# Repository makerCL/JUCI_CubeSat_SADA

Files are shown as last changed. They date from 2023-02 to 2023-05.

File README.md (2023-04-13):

## CubeSat Solar Array Drive - Cal Poly Senior Project

This repository presents the development and proposed design of a deployable Solar Array Drive Assembly that could be flown on space-bound CubeSat missions. Our project addresses the need for reliable sources of power in spacecraft and other missions beyond the Earth's atmosphere. Our goal is to create a two degree of freedom SADA, including the passive retainment, deployment, and axial rotation of a solar array to track the sun during the CubeSat’s orbit. It will have the ability to be easily adapted and integrated into other CubeSat builds but does not include other subsystems necessary for full satellite. The scope includes three main areas: the design and manufacture of a 90-degree locking hinge that allows multiple solar arrays to deploy from the stored launch state, the controlled axial rotation of the deployed panels, and the electronics necessary to manage these features with the potential for sun tracking algorithms. 

Subsystem Managers:
- Miles - Electronics
- Gavin - Software
- James - Project Management
- Kory  - Mechanical
- Jose  - Mechanical

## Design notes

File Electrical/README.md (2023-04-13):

This file details the electrical subsystems
Author: Miles Alderman

##Boards:
- Photodiode Breakout: used for sun sensing with one connected to each solar array
- Pico Shield: Peripherals and connection points that interfaces with a Raspberry Pi Pico

##Accessing the Files
- all project files are in Kicad version 6, which the use will need to use to view them
- Digikey library was imported, available at https://forum.digikey.com/t/importing-the-digi-key-kicad-library-into-kicad-5-0-0/4075
- Custom schematic symbols and footprints are in the "KiCad Libs" folder. These will need to be imported

#SADA Board

##Description
The "SADA BOARD" encompasses all the functionality necessary for the Solar Array Drive Assembly and its components. It would interface with a "Systems Board" through a protocol like I2C or CAN.

##Functionality
- Voltage regulator accepts between 3.7 to 4.2V from an external power supply, which represents a single parallel group of Lithium Ion cells, as would like be present in a CubeSat since about 66% of nano and pico scale satellites implement them.(Bouwmeester and Guo). A battery and battery management system is out of scope for this project.
- Nichrome Wire burner: to burn the fishing line that passively retains the spring-loaded solar arrays, we use Nichrome burn wire. This is necessary since the satellite must be powered off during launch. There are pins used to control the burn signal, one of which is the enable for the PMIC, the other of which controls a Mosfet for connecting power to the Nichrome. In some tests, we found that when the system was powered up from its launch state, if the power supply was turned on with a direct connection to the wire it heated it slower, resulting in less reliable deployment. By having a transistor, we can allow the PMIC to become fully stable, and then open it to heat the wire. This PMIC can then be disable to save power after the wire is burnt. Our tests foudn that about 1.5A was the minimum current to heat the wire enough to cleanly burn the fishing line.
- Attitude Determination Diodes: since in a full CubeSat build there would need to be orientation photodiodes on each corner, the peripherals are provided to do so. This includes a MUX to an ADC channel of the MCU to take this measurement.
    - The photodiodes were connected in reverse bias to the inverting input of an op amp. To take a reading with good resolution, this tiny current must be amplified before reaching an ADC. Transconductance amplifiers are a way to do this, connecting the photodiode to the inverting input of an op-amp, the non-inverting input to ground, and placing a feedback resistor from inverting input to output. A capacitor in parallel with the feedback resistor adds stability by acting as a voltage buffer. Capacitance in the photodiode combined with the feedback resistor naturally create a low pass filter as well. The output voltage of the amplifier can then be connected to an ADC channel of the MCU. The voltage sent to the ADC channel is equal to the photodiode current times the feedback resistor plus the offset voltage at the non-inverting input.
    - It is important to verify the photodiode current is at least an order of magnitude more than the input bias current of the op amp, which roughly doubles with ever 10 deg C increase in temperature.
- Stepper Motor Drivers: Since the stepper motors for axial rotation of the arrays need to be driven from the MCU, a Darlington Transistor array is used to accomplish this. This allows the small current of the MCU GPIO to drive the much higher current needed by a stepper, taken from the 5V supply. Stepper motors are precise, but very power hungry due to _________, so we decided to have MOSFETS that can disconnect from power for when the steppers are not actively changed. This does eliminate some functionality of the steppers, such as fractional stepping, but the resolution of that is far greater than our sensing method's, and thus we couldn't take advantage of it anywyas.
- Breakout board connectors: connectors to the Photodiode Breakout Board are implemented for 2 MUX pins, an ADC channel, power and ground

##Design Considerations 
For full information, please see current design report in the parent folder of the repository. Some key details are listed below
- Were not able to use a "space grade" MCU since they are far too expensive for the price point of this project. We therefore are trying to adapt consumer grade MCUs to fit the needs of this project. This would only protect against total radiation experienced from low energy particles, and not against bit flips. In the systems board, TMR would likely be used. 
- Since this is a prototype and will not be launched into space, we aren't going through the rad hardening. It would be silly to spend extra money for a more specific MCU that wouldn’t work anyways. All the other common MCUs have similar temperature ranges besides the ESP32, although its is still not within range of what we expect a CubeSat to encounter
- Dual Modular Redundancy for these systems?
- In a full system, the battery system would output between about 3.6 - 4.2V if a lithium ion cell chemistry was used. We need to step that down to 3.3V for the RP2040. We chose to use an LDO to power the MCU despite them being less efficient than switching regulators since when the LDOs will use less power when considering the high amount of sleep time of the MCU.
- We decided to use stepper motors despite them being very power hungry. Stepper motors invert  the "locked rotor" issue of dc motors, stepping between locked rotor positions. This means that when the motor is not moving, the coils are still fully energized. This is bad for a CubeSat, where power is extremely scarce. To get around this issue while still utilizing the positional accuracy of stepper motors, we can step the motor and then immediately disconnect the power line so that it stops drawing current. Since the cores of the motor are permenant magnets, the motor remains in the last position even when the motor is off, as long as we do not depend on any partial-stepping functions. 
- USB implemented for the development process, but isn't necessary on a deployed system. It allows the engineer to set it up as a flash device, making it convenient to interface with. The STLINK with SWD and TX/RX pins can be used for all of the functionality in its absence as well. It enables debugging, a serial port, and flashing binary code (such as Micropython) onto the main board.
- The stepper driver boost converters were designed to be able to handle a maximum current of 1A. The stepper motor 28BYJ-48 chosen has a maximum current of approximately 0.28A, so this means that one boost converter could drive 2 motors with a safety factor of 2. This current can easily be increased with minor changes in the supporting circuitry found in the datasheet for the boost converter.
- The darlington transistors were abandoned. They are 45 year old tech, they have pretty substantial current to drive it (power hunger), they have a more substantial voltage drop. Stepper driver chips are much more efficient. 
- Stepper motors were eventually abandoned in favor of a BLDC. https://llis.nasa.gov/lesson/893
- 

SOFTWARE
- NRST Pin exposed to systems board so that software reflash could be triggered externally and passed through I2C instead of SWD. On our board though, we still have teh SWD pins exposed since that is how we will be flashing code. NRST is also helpful as an external reset as it resets the registers and changes the program counter to the reset vector. https://electronics.stackexchange.com/questions/491068/what-is-the-use-of-nrst-pin-in-stm32f401rct6 and p21 of Data sheet

##Citations:
1. J. Bouwmeester, J. Guo, Survey of worldwide pico- and nanosatellite missions, distributions and subsystem technology, Acta Astronautica,
2.  https://www.analog.com/en/technical-articles/optimizing-precision-photodiode-sensor-circuit-design.html

CONCERNS:
- Auxillary photodiode board- if it's just on the panel, it likely will be buffeted with radiation, heat, etc. Need to plan for this

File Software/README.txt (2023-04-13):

The software uses C++ as the compiler. To run code on the Pico, you must first
Download an IDE (I use VS Code) and download a CMake compiler. When writing
software, you first create a main.c file in your working directory, then once
it is written, you have to make a CMakeLists.txt file that includes all the
information CMake needs to compile your code. For reference, look at the 
CMakeLists.txt file in the ADC_Read_script directory. For additional setup, 
refernce this video: https://www.youtube.com/watch?v=B5rQSoOmR5w&ab_channel=Digi-Key
For C++ documentation on the PI, reference the following doxygen pages:
https://raspberrypi.github.io/pico-sdk-doxygen/modules.html

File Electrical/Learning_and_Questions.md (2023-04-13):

## Questions
- separate power supply for ADC?
- is there a difference between power cycling for reset and external reset with NRST pin?
- there seems to be so many different types of resets and conditions... which types matter to us?
- Battery Sag makes Battery input even lower than 3.6V at low SOC?

- Oscillator design
    - Do we need to run this MCU at full speed? (80 MHz)? do we need an external oscillator?
    p11 of oscillator design; Cs is stray capacitance of oscin and oscout pins plus pcb parasitic capacitance

- Double mosfets Too redundant for passive retainment since it only has to work once at the beginning of deployment?
- Clock needs for USB (datasheet p57)
- what would input power be from battery board? Would it be a nominal voltage?
- noise considerations- where are overlapping frequencies? Other design considerations for switching component compatability?
- GIO: which ldo did you use for batt to 3v3 line?

## UPGRADED BOARD
- NRST connected to systems board

## Discussion
- could perhaps use lowpower mode with LSE instead with a lean and mean C code?

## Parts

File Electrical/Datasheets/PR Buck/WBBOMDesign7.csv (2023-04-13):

Part | Manufacturer | Part Number | Quantity | Price ($) | Footprint (mm²) | Description
Rfbb | Vishay-Dale | CRCW0402100KFKED | 1 | 0.01 | 3 | Resistance: 100 kΩ Tolerance: 1.0% Power: 63 mW
Rfbt | Vishay-Dale | CRCW0402232KFKED | 1 | 0.01 | 3 | Resistance: 232 kΩ Tolerance: 1.0% Power: 63 mW
L1 | Vishay-Dale | IHLP1212AEERR22M11 | 1 | 0.63 | 19.32 | L: 220 nH DCR: 11.4 mΩ IDC: 8.5 A
Cin | MuRata | GRM188R60J106ME47D | 2 | 0.03 | 4.68 | Cap: 10 µF Total Derated Cap: 6.6 µF VDC: 6.3 V ESR: 9 mΩ Package: 0603
Cout | MuRata | GRM21BD70J226ME44L | 2 | 0.1 | 6.75 | Cap: 22 µF Total Derated Cap: 38 µF VDC: 6.3 V ESR: 1 mΩ Package: 0805
U1 | Texas Instruments | TPS62867RQYR | 1 | 0.903 | 8.75
Rpgood | Vishay-Dale | CRCW0402100KFKED | 1 | 0.01 | 3 | Resistance: 100 kΩ Tolerance: 1.0% Power: 63 mW

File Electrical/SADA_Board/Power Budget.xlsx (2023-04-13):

Power Budget
Number | Description | Frequency | V_in | Current | Power_total | Efficiency
 | MCU | 8 MHz
 | Passive Retainment Buck | 2.75 MHz
 | Stepper Driver 1 Output
 | Stepper 1 STCK | 1 MHz
 | Stepper Driver 2 Output
 | Stepper 2 STCK | 1 MHz

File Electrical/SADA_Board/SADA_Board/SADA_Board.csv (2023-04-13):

Source: | /Users/milesalderman/Library/CloudStorage/OneDrive-Personal/Documents/Senior Project/JUCI_CubeSat_SADA/Electrical/SADA_Board/SADA_Board/SADA_Board.kicad_sch
Date: | Friday, April 07, 2023 at 02:47:55 PM
Tool: | Eeschema (6.0.11-0)
Generator: | /Applications/KiCad/KiCad.app/Contents/SharedSupport/plugins/bom_csv_grouped_by_value.py
Component Count: | 157
Individual Components:
Item | Qty | Reference(s) | Value | LibPart | Footprint | Datasheet | Category | DK_Datasheet_Link | DK_Detail_Page | Description | Digi-Key_PN | Family | Height | MPN | Manufacturer | Manufacturer_Name | Manufacturer_Part_Number | Mouser Part Number | Mouser Price/Stock | Name | Part | Status
 |  | C1 | 10uF | Device:C | Capacitor_SMD:C_0603_1608Metric | ~ |  |  |  |  |  |  |  | F981A106MMUAJ6
 |  | C2 | 4pF | Device:C | Capacitor_SMD:C_0402_1005Metric | ~ |  |  |  |  |  |  |  | CGA2B2C0G1H060D050BA
 |  | C3 | 100nF | Device:C | Capacitor_SMD:C_0402_1005Metric | ~ |  |  |  |  |  |  |  | GRT155R71C104KE01J
 |  | C4 | 1uF | Device:C | Capacitor_SMD:C_0603_1608Metric | ~ |  |  |  |  |  |  |  | TACL105K016XTA
 |  | C5 | 100nF | Device:C | Capacitor_SMD:C_0402_1005Metric | ~ |  |  |  |  |  |  |  | GRT155R71C104KE01J
 |  | C6 | 100nF | Device:C | Capacitor_SMD:C_0402_1005Metric | ~ |  |  |  |  |  |  |  | GRT155R71C104KE01J
 |  | C7 | 10nF | Device:C | Capacitor_SMD:C_0402_1005Metric | ~ |  |  |  |  |  |  |  | GRT155R71C103KE01J
 |  | C8 | 100nF | Device:C | Capacitor_SMD:C_0402_1005Metric | ~ |  |  |  |  |  |  |  | GRT155R71C104KE01J
 |  | C9 | 4pF | Device:C | Capacitor_SMD:C_0402_1005Metric | ~ |  |  |  |  |  |  |  | CGA2B2C0G1H060D050BA
 |  | C10 | 1nF | Device:C | Resistor_SMD:R_0402_1005Metric | ~ |  |  |  |  |  |  |  | GCM155R71H102KA37J
 |  | C11 | 10nF | Device:C | Capacitor_SMD:C_0402_1005Metric | ~ |  |  |  |  |  |  |  | GRT155R71C103KE01J
 |  | C12 | 10uF | Device:C | Capacitor_SMD:C_0603_1608Metric | ~ |  |  |  |  |  |  |  | GRT188C81A106ME13D
 |  | C13 | 10uF | Device:C | Capacitor_SMD:C_0603_1608Metric | ~ |  |  |  |  |  |  |  | GRT188C81A106ME13D
 |  | C14 | 1.5nF | Device:C | Capacitor_SMD:C_0402_1005Metric | ~ |  |  |  |  |  |  |  | CC0402KRX7R7BB152
 |  | C15 | 10uF | Device:C | Capacitor_SMD:C_0603_1608Metric | ~ |  |  |  |  |  |  |  | GRT188C81A106ME13D
 |  | C16 | 10uF | Device:C | Capacitor_SMD:C_0603_1608Metric | ~ |  |  |  |  |  |  |  | GRT188C81A106ME13D
 |  | C17 | 1uF | Device:C | Capacitor_SMD:C_0603_1608Metric | ~ |  |  |  |  |  |  |  | TACL105K016XTA
 |  | C18 | 1uF | Device:C | Capacitor_SMD:C_0603_1608Metric | ~ |  |  |  |  |  |  |  | TACL105K016XTA
 |  | C19 | 22 uF | Device:C | Capacitor_SMD:C_1210_3225Metric | ~ |  |  |  |  |  |  |  | CGA6P1X7R1C226M250AC |  |  |  |  |  |  | Cout
 |  | C20 | 2.2 uF | Device:C | Resistor_SMD:R_0603_1608Metric | ~ |  |  |  |  |  |  |  | CGA3E1X7S1C225M080AC
 |  | C21 | 22nF | Device:C | Capacitor_SMD:C_0402_1005Metric | ~ |  |  |  |  |  |  |  | AC0402KRX7R7BB223
 |  | C22 | 1nF | Device:C | Resistor_SMD:R_0402_1005Metric | ~ |  |  |  |  |  |  |  | GCM155R71H102KA37J
 |  | C23 | 10nF | Device:C | Resistor_SMD:R_0402_1005Metric | ~ |  |  |  |  |  |  |  | GRT155R71C103KE01J |  |  |  |  |  |  | Cen
 |  | C24 | 22 uF | Device:C | Capacitor_SMD:C_1210_3225Metric | ~ |  |  |  |  |  |  |  | CGA6P1X7R1C226M250AC |  |  |  |  |  |  | Cout
 |  | C25 | 2.2 uF | Device:C | Resistor_SMD:R_0603_1608Metric | ~ |  |  |  |  |  |  |  | CGA3E1X7S1C225M080AC
 |  | C26 | 22nF | Device:C | Capacitor_SMD:C_0402_1005Metric | ~ |  |  |  |  |  |  |  | AC0402KRX7R7BB223
 |  | C27 | 1nF | Device:C | Resistor_SMD:R_0402_1005Metric | ~ |  |  |  |  |  |  |  | GCM155R71H102KA37J
 |  | C28 | 10nF | Device:C | Resistor_SMD:R_0402_1005Metric | ~ |  |  |  |  |  |  |  | GRT155R71C103KE01J |  |  |  |  |  |  | Cen
 |  | C29 | 10uF | Device:C | Capacitor_SMD:C_0603_1608Metric | ~ |  |  |  |  |  |  |  | GRT188C81A106ME13D
 |  | C30 | 10uF | Device:C | Capacitor_SMD:C_0603_1608Metric | ~ |  |  |  |  |  |  |  | GRT188C81A106ME13D
 |  | C31 | 22 uF | Device:C | Capacitor_SMD:C_1210_3225Metric | ~ |  |  |  |  |  |  |  | CGA6P1X7R1C226M250AC |  |  |  |  |  |  | Cout
 |  | C32 | 22 uF | Device:C | Capacitor_SMD:C_1210_3225Metric | ~ |  |  |  |  |  |  |  | CGA6P1X7R1C226M250AC |  |  |  |  |  |  | Cout
 |  | C33 | 100nF | Device:C | Capacitor_SMD:C_0402_1005Metric | ~ |  |  |  |  |  |  |  | GRT155R71C104KE01J
 |  | C34 | 22 uF | Device:C | Capacitor_SMD:C_1210_3225Metric | ~ |  |  |  |  |  |  |  | CGA6P1X7R1C226M250AC |  |  |  |  |  |  | Cout
 |  | C35 | 100nF | Device:C | Capacitor_SMD:C_0402_1005Metric | ~ |  |  |  |  |  |  |  | GRT155R71C104KE01J
 |  | D1 | TVS | Diode:ESD5Zxx | Diode_SMD:D_0402_1005Metric | https://www.onsemi.com/pdf/datasheet/esd5z2.5t1-d.pdf |  |  |  |  |  |  |  | ESD321DPYR
 |  | D2 | TVS | Diode:ESD5Zxx | Diode_SMD:D_0402_1005Metric | https://www.onsemi.com/pdf/datasheet/esd5z2.5t1-d.pdf |  |  |  |  |  |  |  | ESD321DPYR
 |  | D3 | TVS | Diode:ESD5Zxx | Diode_SMD:D_0402_1005Metric | https://www.onsemi.com/pdf/datasheet/esd5z2.5t1-d.pdf |  |  |  |  |  |  |  | ESD321DPYR
 |  | D4 | TVS | Diode:ESD5Zxx | Diode_SMD:D_0402_1005Metric | https://www.onsemi.com/pdf/datasheet/esd5z2.5t1-d.pdf |  |  |  |  |  |  |  | ESD321DPYR
 |  | D5 | TVS | Diode:ESD5Zxx | Diode_SMD:D_0402_1005Metric | https://www.onsemi.com/pdf/datasheet/esd5z2.5t1-d.pdf |  |  |  |  |  |  |  | ESD321DPYR
 |  | D6 | TVS | Diode:ESD5Zxx | Diode_SMD:D_0402_1005Metric | https://www.onsemi.com/pdf/datasheet/esd5z2.5t1-d.pdf |  |  |  |  |  |  |  | ESD321DPYR
 |  | D7 | TVS | Diode:ESD5Zxx | Diode_SMD:D_0402_1005Metric | https://www.onsemi.com/pdf/datasheet/esd5z2.5t1-d.pdf |  |  |  |  |  |  |  | ESD321DPYR
 |  | D8 | TVS | Diode:ESD5Zxx | Diode_SMD:D_0402_1005Metric | https://www.onsemi.com/pdf/datasheet/esd5z2.5t1-d.pdf |  |  |  |  |  |  |  | ESD321DPYR
 |  | D9 | TVS | Diode:ESD5Zxx | Diode_SMD:D_0402_1005Metric | https://www.onsemi.com/pdf/datasheet/esd5z2.5t1-d.pdf |  |  |  |  |  |  |  | ESD321DPYR
 |  | D10 | TVS | Diode:ESD5Zxx | Diode_SMD:D_0402_1005Metric | https://www.onsemi.com/pdf/datasheet/esd5z2.5t1-d.pdf |  |  |  |  |  |  |  | ESD321DPYR
 |  | D11 | TVS | Diode:ESD5Zxx | Diode_SMD:D_0402_1005Metric | https://www.onsemi.com/pdf/datasheet/esd5z2.5t1-d.pdf |  |  |  |  |  |  |  | ESD321DPYR
 |  | D14 | TVS | Diode:ESD5Zxx | Diode_SMD:D_0402_1005Metric | https://www.onsemi.com/pdf/datasheet/esd5z2.5t1-d.pdf |  |  |  |  |  |  |  | ESD321DPYR
 |  | D15 | TVS | Diode:ESD5Zxx | Diode_SMD:D_0402_1005Metric | https://www.onsemi.com/pdf/datasheet/esd5z2.5t1-d.pdf |  |  |  |  |  |  |  | ESD321DPYR
 |  | D16 | TVS | Diode:ESD5Zxx | Diode_SMD:D_0402_1005Metric | https://www.onsemi.com/pdf/datasheet/esd5z2.5t1-d.pdf |  |  |  |  |  |  |  | ESD321DPYR
 |  | D17 | TVS | Diode:ESD5Zxx | Diode_SMD:D_0402_1005Metric | https://www.onsemi.com/pdf/datasheet/esd5z2.5t1-d.pdf |  |  |  |  |  |  |  | ESD321DPYR
 |  | D18 | TVS | Diode:ESD5Zxx | Diode_SMD:D_0402_1005Metric | https://www.onsemi.com/pdf/datasheet/esd5z2.5t1-d.pdf |  |  |  |  |  |  |  | ESD321DPYR
 |  | D19 | TVS | Diode:ESD5Zxx | Diode_SMD:D_0402_1005Metric | https://www.onsemi.com/pdf/datasheet/esd5z2.5t1-d.pdf |  |  |  |  |  |  |  | ESD321DPYR
 |  | D20 | TVS | Diode:ESD5Zxx | Diode_SMD:D_0402_1005Metric | https://www.onsemi.com/pdf/datasheet/esd5z2.5t1-d.pdf |  |  |  |  |  |  |  | ESD321DPYR
 |  | D21 | TVS | Diode:ESD5Zxx | Diode_SMD:D_0402_1005Metric | https://www.onsemi.com/pdf/datasheet/esd5z2.5t1-d.pdf |  |  |  |  |  |  |  | ESD321DPYR
 |  | D22 | TVS | Diode:ESD5Zxx | Diode_SMD:D_0402_1005Metric | https://www.onsemi.com/pdf/datasheet/esd5z2.5t1-d.pdf |  |  |  |  |  |  |  | ESD321DPYR
 |  | D23 | TVS | Diode:ESD5Zxx | Diode_SMD:D_0402_1005Metric | https://www.onsemi.com/pdf/datasheet/esd5z2.5t1-d.pdf |  |  |  |  |  |  |  | ESD321DPYR
 |  | D24 | TVS | Diode:ESD5Zxx | Diode_SMD:D_0402_1005Metric | https://www.onsemi.com/pdf/datasheet/esd5z2.5t1-d.pdf |  |  |  |  |  |  |  | ESD321DPYR
 |  | D25 | TVS | Diode:ESD5Zxx | Diode_SMD:D_0402_1005Metric | https://www.onsemi.com/pdf/datasheet/esd5z2.5t1-d.pdf |  |  |  |  |  |  |  | ESD321DPYR
 |  | D26 | TVS | Diode:ESD5Zxx | Diode_SMD:D_0402_1005Metric | https://www.onsemi.com/pdf/datasheet/esd5z2.5t1-d.pdf |  |  |  |  |  |  |  | ESD321DPYR
 |  | D27 | TVS | Diode:ESD5Zxx | Diode_SMD:D_0402_1005Metric | https://www.onsemi.com/pdf/datasheet/esd5z2.5t1-d.pdf |  |  |  |  |  |  |  | ESD321DPYR
 |  | D28 | LTST-C193KRKT-5A | dk_LED-Indication-Discrete:LG_R971-KN-1 | LED_SMD:LED_0603_1608Metric | https://dammedia.osram.info/media/resource/hires/osram-dam-2493936/LG%20R971.pdf | Optoelectronics | https://dammedia.osram.info/media/resource/hires/osram-dam-2493936/LG%20R971.pdf | /product-detail/en/osram-opto-semiconductors-inc/LG-R971-KN-1/475-1410-1-ND/1802598 | LED GREEN DIFFUSED 0805 SMD | 475-1410-1-ND | LED Indication - Discrete |  | LTST-C193KRKT-5A | OSRAM Opto Semiconductors Inc. |  |  |  |  |  |  | Active
 |  | EXT1 | Male Conn. | 0_custom:{lt}name{gt} | 0_custom:EXT_no_footprint |  |  |  |  |  |  |  |  | 0014562042
 |  | EXT2 | Male Conn. | 0_custom:{lt}name{gt} | 0_custom:EXT_no_footprint |  |  |  |  |  |  |  |  | 0014562042
 |  | EXT3 | Male Conn. | 0_custom:{lt}name{gt} | 0_custom:EXT_no_footprint |  |  |  |  |  |  |  |  | 0014562042
 |  | EXT4 | Male Connector | 0_custom:{lt}name{gt} | 0_custom:EXT_no_footprint |  |  |  |  |  |  |  |  | 1-353293-6
 |  | EXT5 | Photodiodes (8) | 0_custom:{lt}name{gt} | 0_custom:EXT_no_footprint |  |  |  |  |  |  |  |  | SFH 203 P
 |  | EXT6 | PWR Banana Plugs | 0_custom:{lt}name{gt} | 0_custom:EXT_no_footprint |  |  |  |  |  |  |  |  | 1325-02
 |  | EXT7 | Power Male Connector | 0_custom:{lt}name{gt} | 0_custom:EXT_no_footprint |  |  |  |  |  |  |  |  | 3-640427-2
 |  | EXT8 | Male Conn. | 0_custom:{lt}name{gt} | 0_custom:EXT_no_footprint |  |  |  |  |  |  |  |  | 0014562042
 |  | EXT9 | Male Conn. | 0_custom:{lt}name{gt} | 0_custom:EXT_no_footprint |  |  |  |  |  |  |  |  | 0014562042
 |  | EXT10 | Power Male Connector | 0_custom:{lt}name{gt} | 0_custom:EXT_no_footprint |  |  |  |  |  |  |  |  | 3-640427-2
 |  | H1 | MountingHole_Pad | Mechanical:MountingHole_Pad | MountingHole:MountingHole_2.5mm_Pad | ~
 |  | H2 | MountingHole_Pad | Mechanical:MountingHole_Pad | MountingHole:MountingHole_2.5mm_Pad | ~
 |  | H3 | MountingHole_Pad | Mechanical:MountingHole_Pad | MountingHole:MountingHole_2.5mm_Pad | ~
 |  | H4 | MountingHole_Pad | Mechanical:MountingHole_Pad | MountingHole:MountingHole_2.5mm_Pad | ~
 |  | IC1 | TPS25940LRVCR | TPS25940LRVCR:TPS25940LRVCR | Miles Added:QFN50P300X400X80-21N | http://www.ti.com/lit/gpn/tps25940 |  |  |  | 18V, 5A, 42m eFuse With Integrated Reverse Current Protection and DevSleep Support |  |  | 0.8 | TPS25940LRVCR |  | Texas Instruments | TPS25940LRVCR | 595-TPS25940LRVCR | https://www.mouser.co.uk/ProductDetail/Texas-Instruments/TPS25940LRVCR?qs=1MXlzafEN39JjGbgXDnPBQ%3D%3D
 |  | IC2 | LP5912Q3.3DRVRQ1 | LP5912Q3.3DRVRQ1:LP5912Q3.3DRVRQ1 | Miles Added:SON65P200X200X80-7N | http://www.ti.com/lit/gpn/lp5912-q1 |  |  |  | Automotive 500-mA low-noise low-IQ low-dropout (LDO) linear regulator |  |  | 0.8 | LP5912Q3.3DRVRQ1 |  | Texas Instruments | LP5912Q3.3DRVRQ1 | 595-LP5912Q3.3DRVRQ1 | https://www.mouser.co.uk/ProductDetail/Texas-Instruments/LP5912Q33DRVRQ1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
 |  | J1 | Conn_02x08_Odd_Even | Connector_Generic:Conn_02x08_Odd_Even | Connector_PinHeader_2.00mm:PinHeader_2x08_P2.00mm_Vertical | ~ |  |  |  |  |  |  |  | 3-1734506-1
 |  | J2 | 70543-0108 | 70543-0108:70543-0108 | SHDR4W64P0X254_1X4_1271X508X1181P | https://www.molex.com/pdm_docs/sd/705430108_sd.pdf |  |  |  | Molex SL 70543, 2.54mm Pitch, 4 Way, 1 Row, Straight PCB Header, Through Hole |  |  | 11.81 | 70543-0108 |  | Molex | 70543-0108 | 538-70543-0108 | https://www.mouser.co.uk/ProductDetail/Molex/70543-0108?qs=zq6ruAkl8B6UeJlwQa9M3g%3D%3D
 |  | J3 | 70543-0108 | 70543-0108:70543-0108 | SHDR4W64P0X254_1X4_1271X508X1181P | https://www.molex.com/pdm_docs/sd/705430108_sd.pdf |  |  |  | Molex SL 70543, 2.54mm Pitch, 4 Way, 1 Row, Straight PCB Header, Through Hole |  |  | 11.81 | 70543-0108 |  | Molex | 70543-0108 | 538-70543-0108 | https://www.mouser.co.uk/ProductDetail/Molex/70543-0108?qs=zq6ruAkl8B6UeJlwQa9M3g%3D%3D
 |  | J4 | Conn_01x05 | Connector_Generic:Conn_01x05 | Connector_PinHeader_2.00mm:PinHeader_1x05_P2.00mm_Vertical_SMD_Pin1Left | ~ |  |  |  |  |  |  |  | 2PH1-10-UA-SMT-A
 |  | J5 | 70543-0108 | 70543-0108:70543-0108 | SHDR4W64P0X254_1X4_1271X508X1181P | https://www.molex.com/pdm_docs/sd/705430108_sd.pdf |  |  |  | Molex SL 70543, 2.54mm Pitch, 4 Way, 1 Row, Straight PCB Header, Through Hole |  |  | 11.81 | 70543-0108 |  | Molex | 70543-0108 | 538-70543-0108 | https://www.mouser.co.uk/ProductDetail/Molex/70543-0108?qs=zq6ruAkl8B6UeJlwQa9M3g%3D%3D
 |  | J6 | Conn_01x16 | Connector_Generic:Conn_01x16 | Miles Added:CON16_1X16_DUH_HPI125_TYC | ~ |  |  |  |  |  |  |  | 1-292230-6
 |  | J7 | 105431-1202 | molex_105431-1202:105431-1202 | Miles Added:1054311202 | https://www.molex.com/pdm_docs/sd/1054311202_sd.pdf |  |  |  | Headers & Wire Housings NANO-FIT HDR SMT VT SGL 2CKT 15AU BLK |  |  | 9.7 | 105431-1202 |  | Molex | 105431-1202 | 538-105431-1202 | https://www.mouser.co.uk/ProductDetail/Molex/105431-1202?qs=gZXFycFWdANnW%2Fr9%2F5NMjA%3D%3D
 |  | J8 | 10103594-0001LF | dk_USB-DVI-HDMI-Connectors:10103594-0001LF | digikey-footprints:USB_Micro_B_Female_10103594-0001LF | https://cdn.amphenol-icc.com/media/wysiwyg/files/drawing/10103594.pdf | Connectors, Interconnects | https://cdn.amphenol-icc.com/media/wysiwyg/files/drawing/10103594.pdf | /product-detail/en/amphenol-icc-fci/10103594-0001LF/609-4050-1-ND/2350357 | CONN RCPT USB2.0 MICRO B SMD R/A | 609-4050-1-ND | USB, DVI, HDMI Connectors |  | 10103594-0001LF | Amphenol ICC (FCI) |  |  |  |  |  |  | Active
 |  | J9 | 171973-0004 | 171973-0004:171973-0004 | Miles Added:1719730004 | https://www.molex.com/pdm_docs/sd/1719730004_sd.pdf |  |  |  | MOLEX - 171973-0004 - CONNECTOR, HEADER, 4POS, 1ROW, 2.54MM |  |  | 11.8 | 171973-0004 |  | Molex | 171973-0004 | 538-171973-0004 | https://www.mouser.co.uk/ProductDetail/Molex/171973-0004?qs=lc2O%252BfHJPVaHyBdhjsB7Nw%3D%3D
 |  | J10 | 171973-0004 | 171973-0004:171973-0004 | Miles Added:1719730004 | https://www.molex.com/pdm_docs/sd/1719730004_sd.pdf |  |  |  | MOLEX - 171973-0004 - CONNECTOR, HEADER, 4POS, 1ROW, 2.54MM |  |  | 11.8 | 171973-0004 |  | Molex | 171973-0004 | 538-171973-0004 | https://www.mouser.co.uk/ProductDetail/Molex/171973-0004?qs=lc2O%252BfHJPVaHyBdhjsB7Nw%3D%3D
 |  | J11 | 105431-1202 | molex_105431-1202:105431-1202 | Miles Added:1054311202 | https://www.molex.com/pdm_docs/sd/1054311202_sd.pdf |  |  |  | Headers & Wire Housings NANO-FIT HDR SMT VT SGL 2CKT 15AU BLK |  |  | 9.7 | 105431-1202 |  | Molex | 105431-1202 | 538-105431-1202 | https://www.mouser.co.uk/ProductDetail/Molex/105431-1202?qs=gZXFycFWdANnW%2Fr9%2F5NMjA%3D%3D
 |  | J14 | Conn_01x02 | Connector_Generic:Conn_01x02 | Connector_PinSocket_2.00mm:PinSocket_1x02_P2.00mm_Vertical | ~
 |  | J15 | Conn_01x02 | Connector_Generic:Conn_01x02 | Connector_PinSocket_2.00mm:PinSocket_1x02_P2.00mm_Vertical | ~
 |  | JP1 | Jumper_3_Open | Jumper:Jumper_3_Open | Connector_PinHeader_2.00mm:PinHeader_1x03_P2.00mm_Vertical | ~ |  |  |  |  |  |  |  | 2PH1-10-UA-SMT-A
 |  | L1 | 220 nH | IHLP1212AEERR22M11:IHLP1212AEERR22M11 | Miles Added:INDPM3630X150N | https://datasheet.datasheetarchive.com/originals/distributors/Datasheets-DGA11/2199817.pdf |  |  |  | VISHAY - IHLP1212AEERR22M11 - INDUCTOR, IHLP-1212AE-11, 0.22UH 20% |  |  | 1.5 | IHLP1212AEERR22M11 |  | Vishay | IHLP1212AEERR22M11 | 70-IHLP1212AEERR22M1 | https://www.mouser.co.uk/ProductDetail/Vishay-Dale/IHLP1212AEERR22M11?qs=hVaL6jEgczpS%2FYM%2FgrlwRQ%3D%3D
 |  | Q1 | NVR5198NLT1G | dk_Transistors-FETs-MOSFETs-Single:2N7002 | digikey-footprints:SOT-23-3 | https://www.onsemi.com/pub/Collateral/NDS7002A-D.PDF | Discrete Semiconductor Products | https://www.onsemi.com/pub/Collateral/NDS7002A-D.PDF | /product-detail/en/on-semiconductor/2N7002/2N7002NCT-ND/244664 | MOSFET N-CH 60V 115MA SOT-23 | 2N7002NCT-ND | Transistors - FETs, MOSFETs - Single |  | NVR5198NLT1G | ON Semiconductor |  |  |  |  |  |  | Active
 |  | Q2 | NVR5198NLT1G | dk_Transistors-FETs-MOSFETs-Single:2N7002 | digikey-footprints:SOT-23-3 | https://www.onsemi.com/pub/Collateral/NDS7002A-D.PDF | Discrete Semiconductor Products | https://www.onsemi.com/pub/Collateral/NDS7002A-D.PDF | /product-detail/en/on-semiconductor/2N7002/2N7002NCT-ND/244664 | MOSFET N-CH 60V 115MA SOT-23 | 2N7002NCT-ND | Transistors - FETs, MOSFETs - Single |  | NVR5198NLT1G | ON Semiconductor |  |  |  |  |  |  | Active
 |  | Q3 | IRLML6244TRPBF | IRLML6244TRPBF:IRLML6244TRPBF | SOT95P237X112-3N | http://www.infineon.com/dgdl/irlml6244pbf.pdf?fileId=5546d462533600a4015356686fed261f |  |  |  | INFINEON - IRLML6244TRPBF - MOSFET, N CH, 20V, 6.3A, SOT-23 |  |  | 1.12 | IRLML6244TRPBF |  | Infineon | IRLML6244TRPBF | 942-IRLML6244TRPBF | https://www.mouser.co.uk/ProductDetail/Infineon-Technologies/IRLML6244TRPBF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
 |  | R1 | 4.7k | Device:R_US | Resistor_SMD:R_0402_1005Metric | ~ |  |  |  |  |  |  |  | AC0402FR-134K7L
 |  | R2 | 4.7k | Device:R_US | Resistor_SMD:R_0402_1005Metric | ~ |  |  |  |  |  |  |  | AC0402FR-134K7L
 |  | R3 | 200k | Device:R_US | Resistor_SMD:R_0603_1608Metric_Pad0.98x0.95mm_HandSolder | ~ |  |  |  |  |  |  |  | AC0603FR-07200KL |  |  |  |  |  | Rf
 |  | R4 | 16.8k | Device:R_US | Resistor_SMD:R_0402_1005Metric | ~ |  |  |  |  |  |  |  | AC0402FR-0716K9L
 |  | R5 | 4.7k | Device:R_US | Resistor_SMD:R_0402_1005Metric | ~ |  |  |  |  |  |  |  | AC0402FR-134K7L
 |  | R6 | 100k | Device:R_US | Resistor_SMD:R_0402_1005Metric | ~ |  |  |  |  |  |  |  | RMCF0402FT100K |  |  |  |  |  |  | R_OFF
 |  | R7 | 374k | Device:R_US | Resistor_SMD:R_0402_1005Metric | ~ |  |  |  |  |  |  |  | RC0402FR-07374KL
 |  | R8 | 100k | Device:R_US | Resistor_SMD:R_0402_1005Metric | ~ |  |  |  |  |  |  |  | RMCF0402FT100K |  |  |  |  |  |  | R_OFF
 |  | R9 | 147k | Device:R_US | Resistor_SMD:R_0402_1005Metric | ~ |  |  |  |  |  |  |  | RC0402FR-07147KL
 |  | R10 | 300k | Device:R_US | Resistor_SMD:R_0402_1005Metric | ~ |  |  |  |  |  |  |  | RC0402JR-07300KL
 |  | R11 | 15k | Device:R_US | Resistor_SMD:R_0603_1608Metric | ~ |  |  |  |  |  |  |  | AC0603FR-0715KL
 |  | R12 | 2.2k | Device:R_US | Resistor_SMD:R_0402_1005Metric | ~ |  |  |  |  |  |  |  | AC0402FR-072K2L
 |  | R13 | 18k | Device:R_US | Resistor_SMD:R_0402_1005Metric | ~ |  |  |  |  |  |  |  | AC0402FR-0718KL
 |  | R14 | 18k | Device:R_US | Resistor_SMD:R_0402_1005Metric | ~ |  |  |  |  |  |  |  | AC0402FR-0718KL
 |  | R15 | 18k | Device:R_US | Resistor_SMD:R_0402_1005Metric | ~ |  |  |  |  |  |  |  | AC0402FR-0718KL
 |  | R16 | 330m | Device:R_US | Resistor_SMD:R_1206_3216Metric | ~ |  |  |  |  |  |  |  | KRL1632E-M-R330-F-T5 |  |  |  |  |  |  | R_SNS_B
 |  | R17 | 330m | Device:R_US | Resistor_SMD:R_1206_3216Metric | ~ |  |  |  |  |  |  |  | KRL1632E-M-R330-F-T5 |  |  |  |  |  |  | R_SNS_A
 |  | R18 | 100k | Device:R_US | Resistor_SMD:R_0402_1005Metric | ~ |  |  |  |  |  |  |  | RMCF0402FT100K |  |  |  |  |  |  | R_OFF
 |  | R19 | 1k | Device:R_US | Resistor_SMD:R_0402_1005Metric | ~ |  |  |  |  |  |  |  | AC0402FR-131KL
 |  | R20 | 2.2k | Device:R_US | Resistor_SMD:R_0402_1005Metric | ~ |  |  |  |  |  |  |  | AC0402FR-072K2L
 |  | R21 | 18k | Device:R_US | Resistor_SMD:R_0402_1005Metric | ~ |  |  |  |  |  |  |  | AC0402FR-0718KL
 |  | R22 | 18k | Device:R_US | Resistor_SMD:R_0402_1005Metric | ~ |  |  |  |  |  |  |  | AC0402FR-0718KL
 |  | R23 | 18k | Device:R_US | Resistor_SMD:R_0402_1005Metric | ~ |  |  |  |  |  |  |  | AC0402FR-0718KL
 |  | R24 | 330m | Device:R_US | Resistor_SMD:R_1206_3216Metric | ~ |  |  |  |  |  |  |  | KRL1632E-M-R330-F-T5 |  |  |  |  |  |  | R_SNS_B
 |  | R25 | 330m | Device:R_US | Resistor_SMD:R_1206_3216Metric | ~ |  |  |  |  |  |  |  | KRL1632E-M-R330-F-T5 |  |  |  |  |  |  | R_SNS_A
 |  | R26 | 100k | Device:R_US | Resistor_SMD:R_0402_1005Metric | ~ |  |  |  |  |  |  |  | RMCF0402FT100K |  |  |  |  |  |  | R_OFF
 |  | R27 | 1k | Device:R_US | Resistor_SMD:R_0402_1005Metric | ~ |  |  |  |  |  |  |  | AC0402FR-131KL
 |  | R28 | 200k | Device:R_US | Resistor_SMD:R_0603_1608Metric_Pad0.98x0.95mm_HandSolder | ~ |  |  |  |  |  |  |  | AC0603FR-07200KL
 |  | R29 | 100k | Device:R_US | Resistor_SMD:R_0402_1005Metric | ~ |  |  |  |  |  |  |  | RMCF0402FT100K
 |  | R30 | 100k | Device:R_US | Resistor_SMD:R_0402_1005Metric | ~ |  |  |  |  |  |  |  | RMCF0402FT100K
 |  | R31 | 4.7k | Device:R_US | Resistor_SMD:R_0402_1005Metric | ~ |  |  |  |  |  |  |  | AC0402FR-134K7L
 |  | R32 | 270 | Device:R_US | Resistor_SMD:R_0402_1005Metric | ~ |  |  |  |  |  |  |  | CRGCQ0402F270R
 |  | S1 | KSR253GLFG | KSR253GLFG:KSR253GLFG | KSR253GLFG | https://www.ckswitches.com/media/1466/ksr.pdf |  |  |  | KSR253GLFG (Tactile Switches) |  |  | 2.5 | KSR253GLFG |  | C & K COMPONENTS | KSR253GLFG | 611-KSR253G-LFG | https://www.mouser.co.uk/ProductDetail/CK/KSR253GLFG?qs=vOd3edNlRKDxg8jfKSjxTA%3D%3D
 |  | TP1 | TestPoint | Connector:TestPoint | TestPoint:TestPoint_Pad_D1.0mm | ~
 |  | TP2 | TestPoint | Connector:TestPoint | TestPoint:TestPoint_Pad_D1.0mm | ~
 |  | TP5 | TestPoint | Connector:TestPoint | TestPoint:TestPoint_Pad_D1.0mm | ~
 |  | TP6 | TestPoint | Connector:TestPoint | TestPoint:TestPoint_Pad_D1.0mm | ~
 |  | TP7 | TestPoint | Connector:TestPoint | TestPoint:TestPoint_Pad_D1.0mm | ~
 |  | TP8 | TestPoint | Connector:TestPoint | TestPoint:TestPoint_Pad_D1.0mm | ~
 |  | TP9 | TestPoint | Connector:TestPoint | TestPoint:TestPoint_Pad_D1.0mm | ~
 |  | TP10 | TestPoint | Connector:TestPoint | TestPoint:TestPoint_Pad_D1.0mm | ~
 |  | TP11 | TestPoint | Connector:TestPoint | TestPoint:TestPoint_Pad_D1.0mm | ~
 |  | TP12 | TestPoint | Connector:TestPoint | TestPoint:TestPoint_Pad_D1.0mm | ~
 |  | TP13 | TestPoint | Connector:TestPoint | TestPoint:TestPoint_Pad_D1.0mm | ~
 |  | TP14 | TestPoint | Connector:TestPoint | TestPoint:TestPoint_Pad_D1.0mm | ~
 |  | TP15 | TestPoint | Connector:TestPoint | TestPoint:TestPoint_Pad_D1.0mm | ~
 |  | TP16 | TestPoint | Connector:TestPoint | TestPoint:TestPoint_Pad_D1.0mm | ~
 |  | TP17 | TestPoint | Connector:TestPoint | TestPoint:TestPoint_Pad_D1.0mm | ~
 |  | TP18 | TestPoint | Connector:TestPoint | TestPoint:TestPoint_Pad_D1.0mm | ~
 |  | TP19 | TestPoint | Connector:TestPoint | TestPoint:TestPoint_Pad_D1.0mm | ~
 |  | TP20 | TestPoint | Connector:TestPoint | TestPoint:TestPoint_Pad_D1.0mm | ~
 |  | TP21 | TestPoint | Connector:TestPoint | TestPoint:TestPoint_Pad_D1.0mm | ~
 |  | U1 | STM32L476RGTx | MCU_ST_STM32L4:STM32L476RGTx | Package_QFP:LQFP-64_10x10mm_P0.5mm | http://www.st.com/st-web-ui/static/active/en/resource/technical/document/datasheet/DM00108832.pdf |  |  |  |  |  |  |  | STM32L476RGT3
 |  | U2 | CD4051B | Analog_Switch:CD4051B | Miles Added:PW0016A_L | http://www.ti.com/lit/ds/symlink/cd4052b.pdf |  |  |  |  |  |  |  | CD4051BQPWRG4Q1
 |  | U3 | LM321 | Amplifier_Operational:LMV321 | Package_TO_SOT_SMD:SOT-23-5 | https://www.ti.com/general/docs/suppproductinfo.tsp?distId=10 |  |  |  |  |  |  |  | LM321LVIDBVR
 |  | U4 | NCV68261MTWAITBG | :NCV68261MTWAITBG_1 | Miles Added:WDFNW6_511DW_ONS_OSI | NCV68261MTWAITBG |  |  |  |  |  |  |  | NCV68261MTWAITBG
 |  | U5 | NCV68261MTWAITBG | :NCV68261MTWAITBG_1 | Miles Added:WDFNW6_511DW_ONS_OSI | NCV68261MTWAITBG |  |  |  |  |  |  |  | NCV68261MTWAITBG
 |  | U6 | STSPIN220 | Driver_Motor:STSPIN220 | Package_DFN_QFN:VQFN-16-1EP_3x3mm_P0.5mm_EP1.8x1.8mm | www.st.com/resource/en/datasheet/stspin220.pdf |  |  |  |  |  |  |  | STSPIN220
 |  | U7 | STSPIN220 | Driver_Motor:STSPIN220 | Package_DFN_QFN:VQFN-16-1EP_3x3mm_P0.5mm_EP1.8x1.8mm | www.st.com/resource/en/datasheet/stspin220.pdf |  |  |  |  |  |  |  | STSPIN220
 |  | U8 | TPS62867RQYR | 0_custom:TPS62867RQYR | 0_custom:VQFN-9 |  |  |  |  |  |  |  |  | TPS62867RQYR
 |  | U11 | USBLC6-2SC6 | Power_Protection:USBLC6-2SC6 | Package_TO_SOT_SMD:SOT-23-6 | https://www.st.com/resource/en/datasheet/usblc6-2.pdf |  |  |  |  |  |  |  | USBLC6-2SC6
 |  | Y1 | ECS_Chrystal_ | 0_custom:ECS_Chrystal_ | Miles Added:XTAL_ECS-160-8-36Q-AES-TR | https://www.mouser.com/datasheet/2/122/ECX_2236Q-938171.pdf |  |  |  |  |  |  |  | ECS-160-8-36Q-AES-TR
Collated Components:
Item | Qty | Reference(s) | Value | LibPart | Footprint | Datasheet | Category | DK_Datasheet_Link | DK_Detail_Page | Description | Digi-Key_PN | Family | Height | MPN | Manufacturer | Manufacturer_Name | Manufacturer_Part_Number | Mouser Part Number | Mouser Price/Stock | Name | Part | Status
1 | 7 | C1, C12, C13, C15, C16, C29, C30 | 10uF | Device:C | Capacitor_SMD:C_0603_1608Metric | ~ |  |  |  |  |  |  |  | F981A106MMUAJ6
2 | 2 | C2, C9 | 4pF | Device:C | Capacitor_SMD:C_0402_1005Metric | ~ |  |  |  |  |  |  |  | CGA2B2C0G1H060D050BA
3 | 6 | C3, C5, C6, C8, C33, C35 | 100nF | Device:C | Capacitor_SMD:C_0402_1005Metric | ~ |  |  |  |  |  |  |  | GRT155R71C104KE01J
4 | 3 | C4, C17, C18 | 1uF | Device:C | Capacitor_SMD:C_0603_1608Metric | ~ |  |  |  |  |  |  |  | TACL105K016XTA
5 | 2 | C7, C11 | 10nF | Device:C | Capacitor_SMD:C_0402_1005Metric | ~ |  |  |  |  |  |  |  | GRT155R71C103KE01J
6 | 3 | C10, C22, C27 | 1nF | Device:C | Resistor_SMD:R_0402_1005Metric | ~ |  |  |  |  |  |  |  | GCM155R71H102KA37J
7 | 1 | C14 | 1.5nF | Device:C | Capacitor_SMD:C_0402_1005Metric | ~ |  |  |  |  |  |  |  | CC0402KRX7R7BB152
8 | 5 | C19, C24, C31, C32, C34 | 22 uF | Device:C | Capacitor_SMD:C_1210_3225Metric | ~ |  |  |  |  |  |  |  | CGA6P1X7R1C226M250AC |  |  |  |  |  |  | Cout
9 | 2 | C20, C25 | 2.2 uF | Device:C | Resistor_SMD:R_0603_1608Metric | ~ |  |  |  |  |  |  |  | CGA3E1X7S1C225M080AC
10 | 2 | C21, C26 | 22nF | Device:C | Capacitor_SMD:C_0402_1005Metric | ~ |  |  |  |  |  |  |  | AC0402KRX7R7BB223
11 | 2 | C23, C28 | 10nF | Device:C | Resistor_SMD:R_0402_1005Metric | ~ |  |  |  |  |  |  |  | GRT155R71C103KE01J |  |  |  |  |  |  | Cen
12 | 25 | D1, D2, D3, D4, D5, D6, D7, D8, D9, D10, D11, D14, D15, D16, D17, D18, D19, D20, D21, D22, D23, D24, D25, D26, D27 | TVS | Diode:ESD5Zxx | Diode_SMD:D_0402_1005Metric | https://www.onsemi.com/pdf/datasheet/esd5z2.5t1-d.pdf |  |  |  |  |  |  |  | ESD321DPYR
13 | 1 | D28 | LTST-C193KRKT-5A | dk_LED-Indication-Discrete:LG_R971-KN-1 | LED_SMD:LED_0603_1608Metric | https://dammedia.osram.info/media/resource/hires/osram-dam-2493936/LG%20R971.pdf | Optoelectronics | https://dammedia.osram.info/media/resource/hires/osram-dam-2493936/LG%20R971.pdf | /product-detail/en/osram-opto-semiconductors-inc/LG-R971-KN-1/475-1410-1-ND/1802598 | LED GREEN DIFFUSED 0805 SMD | 475-1410-1-ND | LED Indication - Discrete |  | LTST-C193KRKT-5A | OSRAM Opto Semiconductors Inc. |  |  |  |  |  |  | Active
14 | 5 | EXT1, EXT2, EXT3, EXT8, EXT9 | Male Conn. | 0_custom:{lt}name{gt} | 0_custom:EXT_no_footprint |  |  |  |  |  |  |  |  | 0014562042
15 | 1 | EXT4 | Male Connector | 0_custom:{lt}name{gt} | 0_custom:EXT_no_footprint |  |  |  |  |  |  |  |  | 1-353293-6
16 | 1 | EXT5 | Photodiodes (8) | 0_custom:{lt}name{gt} | 0_custom:EXT_no_footprint |  |  |  |  |  |  |  |  | SFH 203 P
17 | 1 | EXT6 | PWR Banana Plugs | 0_custom:{lt}name{gt} | 0_custom:EXT_no_footprint |  |  |  |  |  |  |  |  | 1325-02
18 | 2 | EXT7, EXT10 | Power Male Connector | 0_custom:{lt}name{gt} | 0_custom:EXT_no_footprint |  |  |  |  |  |  |  |  | 3-640427-2
19 | 4 | H1, H2, H3, H4 | MountingHole_Pad | Mechanical:MountingHole_Pad | MountingHole:MountingHole_2.5mm_Pad | ~
20 | 1 | IC1 | TPS25940LRVCR | TPS25940LRVCR:TPS25940LRVCR | Miles Added:QFN50P300X400X80-21N | http://www.ti.com/lit/gpn/tps25940 |  |  |  | 18V, 5A, 42m eFuse With Integrated Reverse Current Protection and DevSleep Support |  |  | 0.8 | TPS25940LRVCR |  | Texas Instruments | TPS25940LRVCR | 595-TPS25940LRVCR | https://www.mouser.co.uk/ProductDetail/Texas-Instruments/TPS25940LRVCR?qs=1MXlzafEN39JjGbgXDnPBQ%3D%3D
21 | 1 | IC2 | LP5912Q3.3DRVRQ1 | LP5912Q3.3DRVRQ1:LP5912Q3.3DRVRQ1 | Miles Added:SON65P200X200X80-7N | http://www.ti.com/lit/gpn/lp5912-q1 |  |  |  | Automotive 500-mA low-noise low-IQ low-dropout (LDO) linear regulator |  |  | 0.8 | LP5912Q3.3DRVRQ1 |  | Texas Instruments | LP5912Q3.3DRVRQ1 | 595-LP5912Q3.3DRVRQ1 | https://www.mouser.co.uk/ProductDetail/Texas-Instruments/LP5912Q33DRVRQ1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
22 | 1 | J1 | Conn_02x08_Odd_Even | Connector_Generic:Conn_02x08_Odd_Even | Connector_PinHeader_2.00mm:PinHeader_2x08_P2.00mm_Vertical | ~ |  |  |  |  |  |  |  | 3-1734506-1
23 | 3 | J2, J3, J5 | 70543-0108 | 70543-0108:70543-0108 | SHDR4W64P0X254_1X4_1271X508X1181P | https://www.molex.com/pdm_docs/sd/705430108_sd.pdf |  |  |  | Molex SL 70543, 2.54mm Pitch, 4 Way, 1 Row, Straight PCB Header, Through Hole |  |  | 11.81 | 70543-0108 |  | Molex | 70543-0108 | 538-70543-0108 | https://www.mouser.co.uk/ProductDetail/Molex/70543-0108?qs=zq6ruAkl8B6UeJlwQa9M3g%3D%3D
24 | 1 | J4 | Conn_01x05 | Connector_Generic:Conn_01x05 | Connector_PinHeader_2.00mm:PinHeader_1x05_P2.00mm_Vertical_SMD_Pin1Left | ~ |  |  |  |  |  |  |  | 2PH1-10-UA-SMT-A
25 | 1 | J6 | Conn_01x16 | Connector_Generic:Conn_01x16 | Miles Added:CON16_1X16_DUH_HPI125_TYC | ~ |  |  |  |  |  |  |  | 1-292230-6
26 | 2 | J7, J11 | 105431-1202 | molex_105431-1202:105431-1202 | Miles Added:1054311202 | https://www.molex.com/pdm_docs/sd/1054311202_sd.pdf |  |  |  | Headers & Wire Housings NANO-FIT HDR SMT VT SGL 2CKT 15AU BLK |  |  | 9.7 | 105431-1202 |  | Molex | 105431-1202 | 538-105431-1202 | https://www.mouser.co.uk/ProductDetail/Molex/105431-1202?qs=gZXFycFWdANnW%2Fr9%2F5NMjA%3D%3D
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

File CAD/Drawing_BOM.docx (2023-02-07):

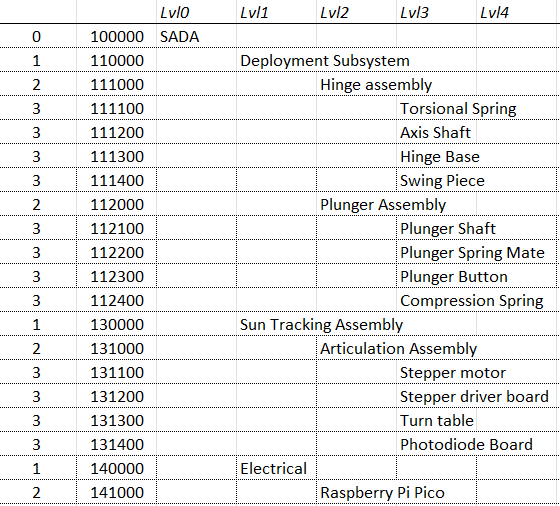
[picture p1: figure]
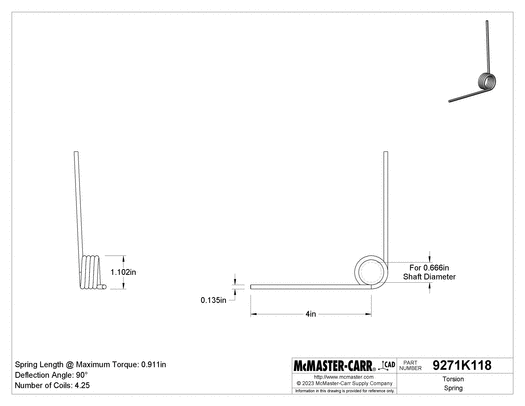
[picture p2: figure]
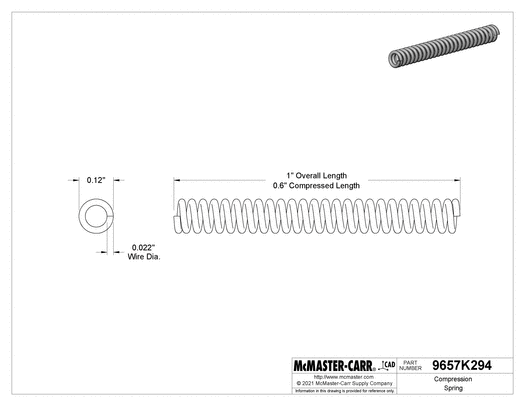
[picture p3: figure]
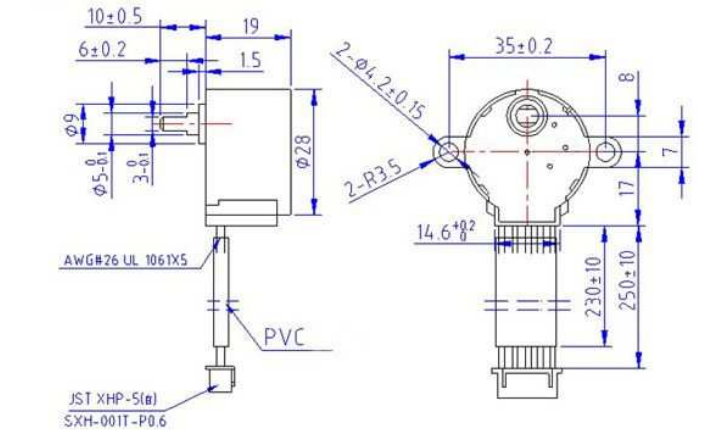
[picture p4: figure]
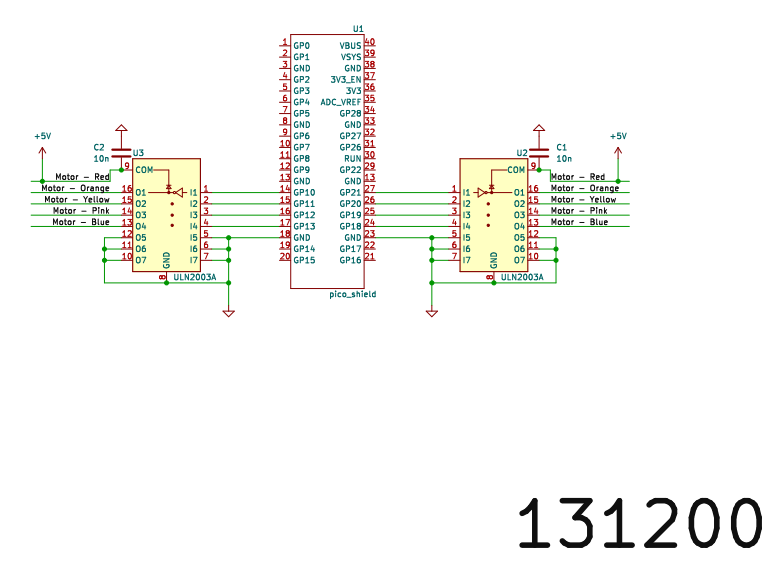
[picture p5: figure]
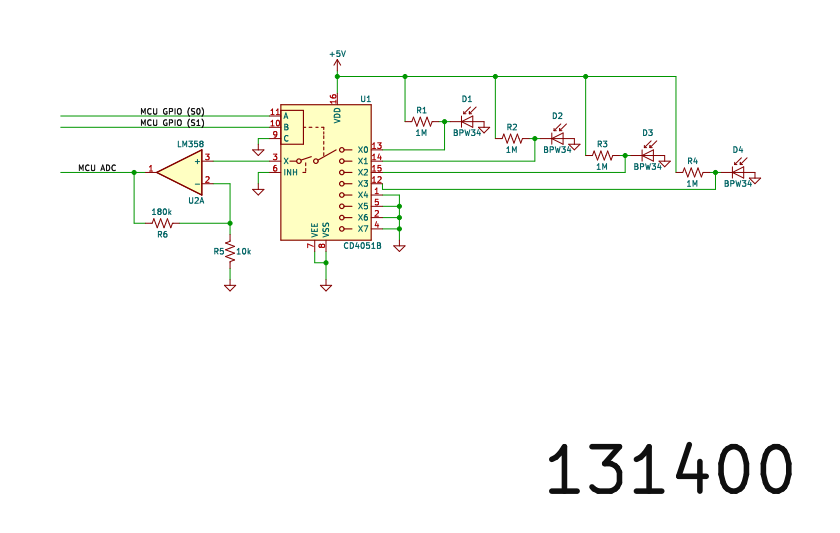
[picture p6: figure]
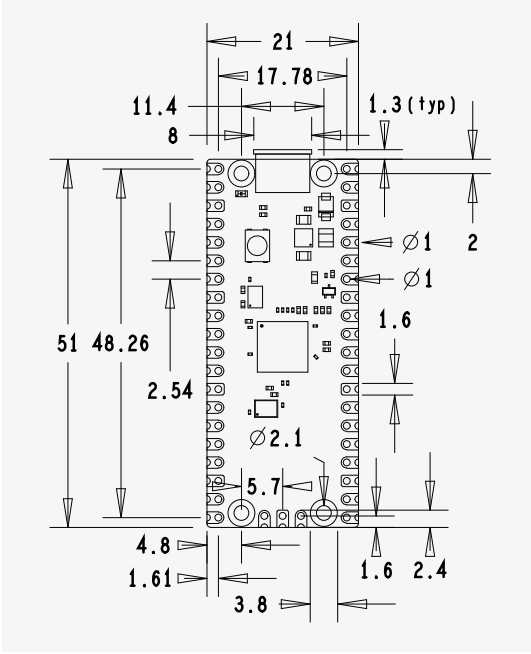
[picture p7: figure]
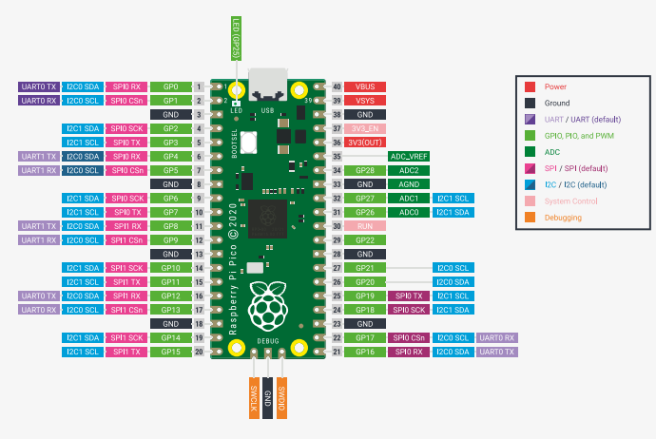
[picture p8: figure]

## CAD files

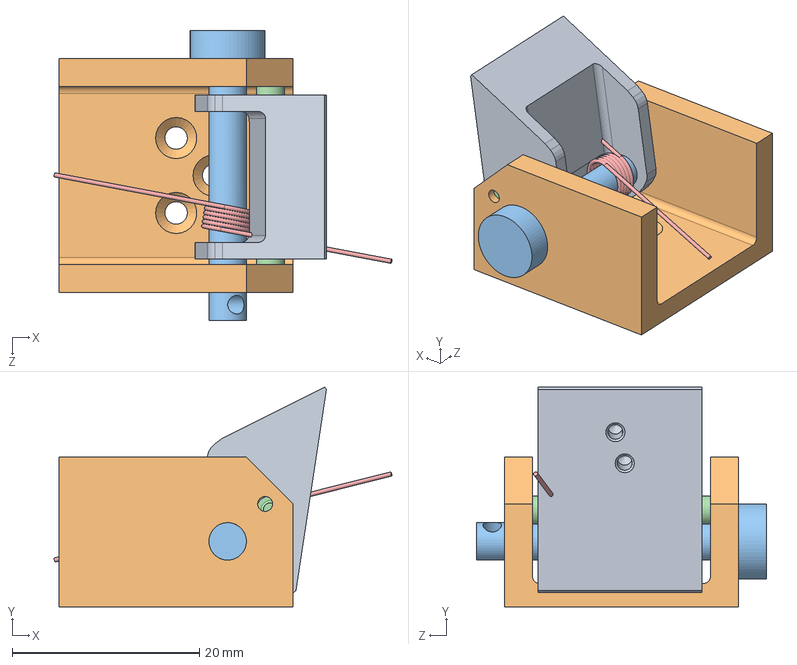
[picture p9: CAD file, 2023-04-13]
CAD/Hinge redesign 2/Assem2.SLDASM
36.1 x 23.5 x 31.0 mm
Swing piece better redesign v2
Base better redesign
Hinge mcmaster 4mm
Pin mcmaster_v2 x 2

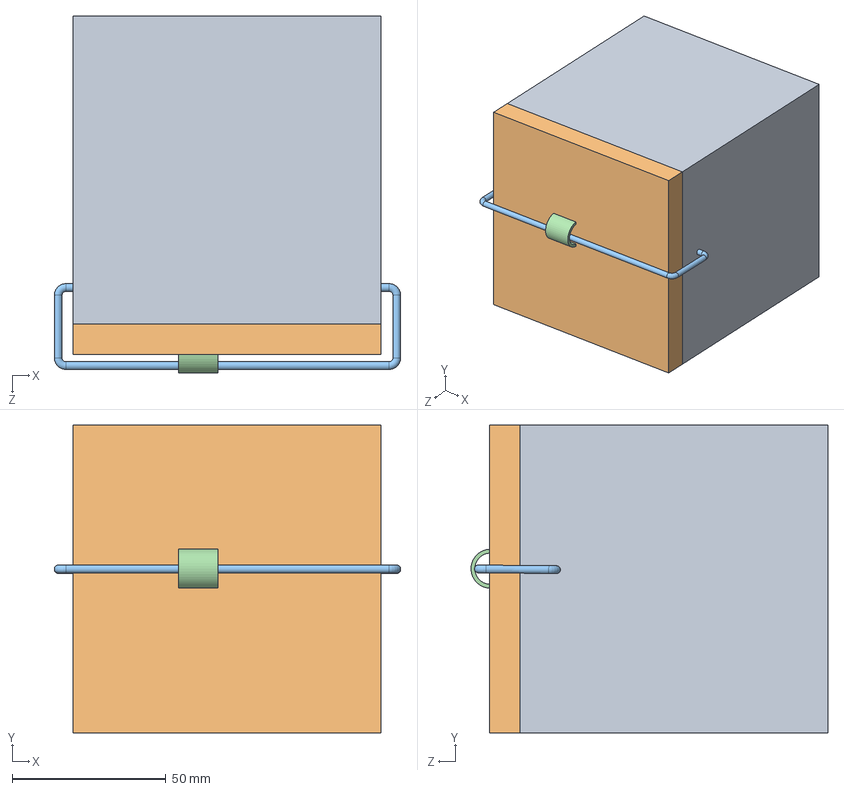
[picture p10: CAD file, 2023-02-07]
CAD/Passive Retainment/Retainment ASM.SLDASM
112.5 x 100.0 x 116.0 mm
CubeSat
Deployable
Fishing Line
Nichrome Wire

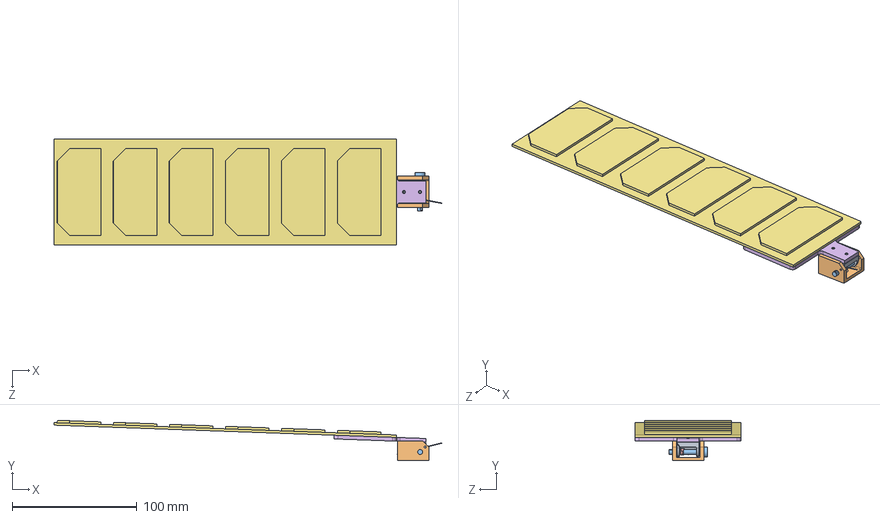
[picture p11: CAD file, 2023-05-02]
CAD/Bracket+Hinge assembly/Bracket_Assembly_V1.SLDASM
311.5 x 32.5 x 85.0 mm
Swing_Piece_V1
Base better redesign
Bolt_mcmaster_V1
Locking_Pin_mcmaster_V1 x 2
Array HolderV2
Solar Panel

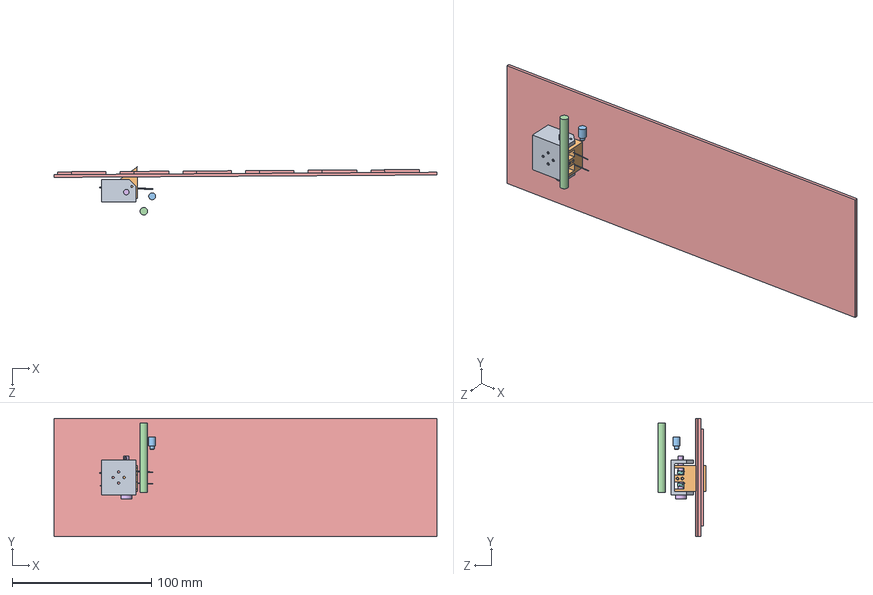
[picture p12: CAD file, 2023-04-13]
CAD/Hinge redesign 2/Assembly1.SLDASM
275.0 x 85.0 x 34.6 mm
Base better redesign
Swing piece better redesign
Hinge mcmaster 4mm
Pin mcmaster_v2
9271K88_Torsion Spring x 2

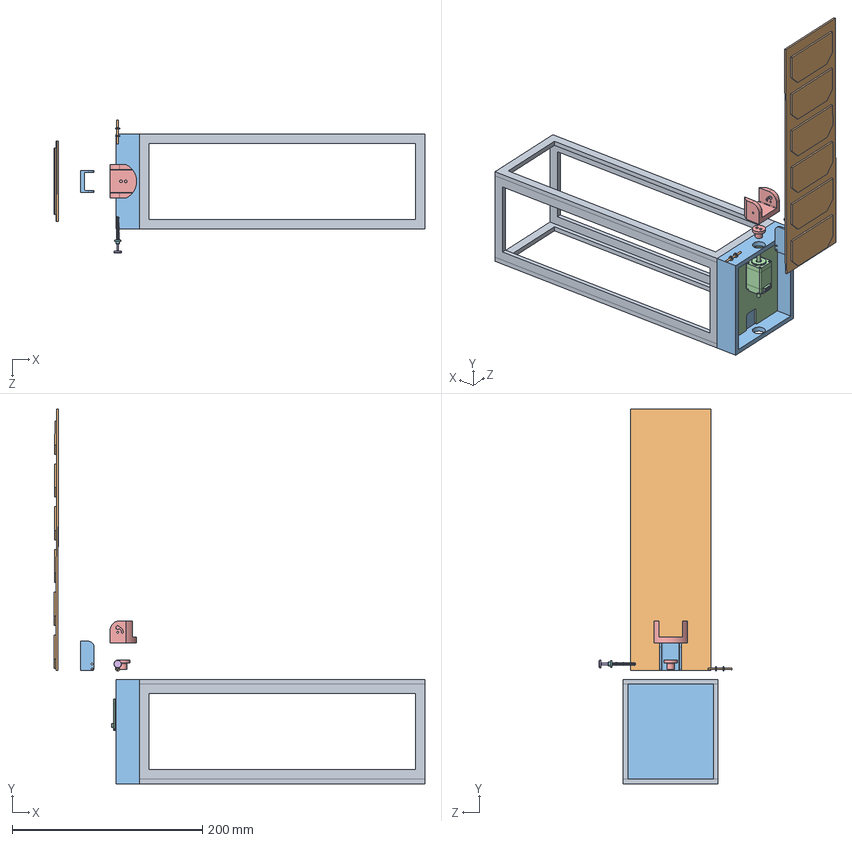
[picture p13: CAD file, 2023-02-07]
CAD/PDR Idea/SADA ASM.SLDASM
390.1 x 394.0 x 139.3 mm
side panel x 4
Solar Panel
Motor Housing
PCB
Base
Plunger Button
Plunger Spring Shaft
Plunger Spring-Button Mate
9657K294_Compression Spring
Axis Shaft
Swing Piece
6627T33_Stepper Motor
Turn Table

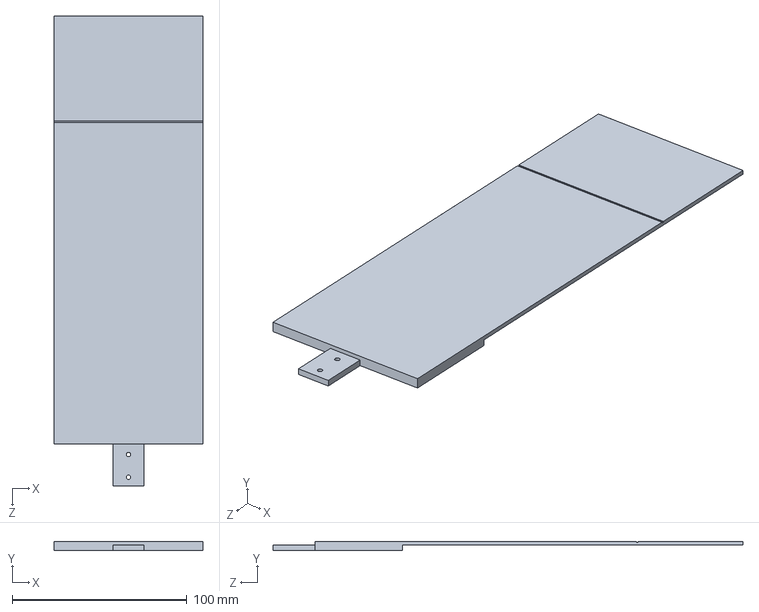
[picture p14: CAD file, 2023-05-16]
CAD/Bracket+Hinge assembly/Solar Panel + Bracket.SLDPRT
85.0 x 5.00 x 269.0 mm

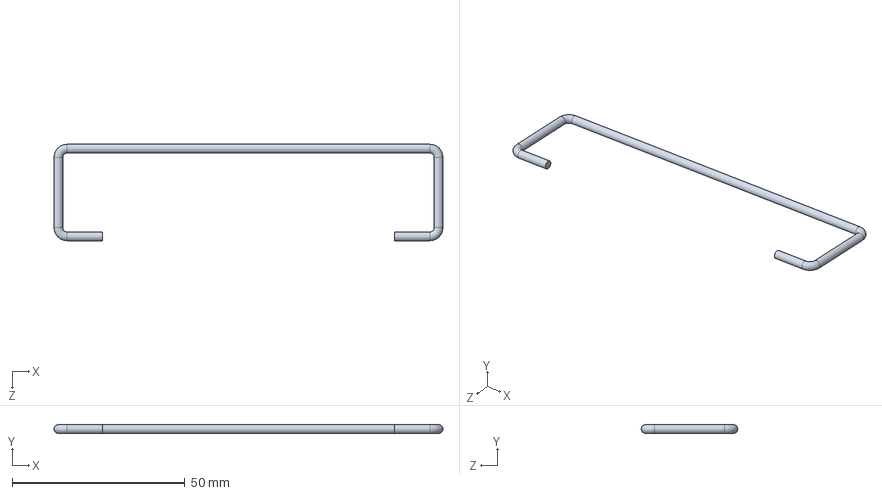
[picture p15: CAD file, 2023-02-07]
CAD/Passive Retainment/Fishing Line.SLDPRT
112.5 x 2.54 x 27.9 mm

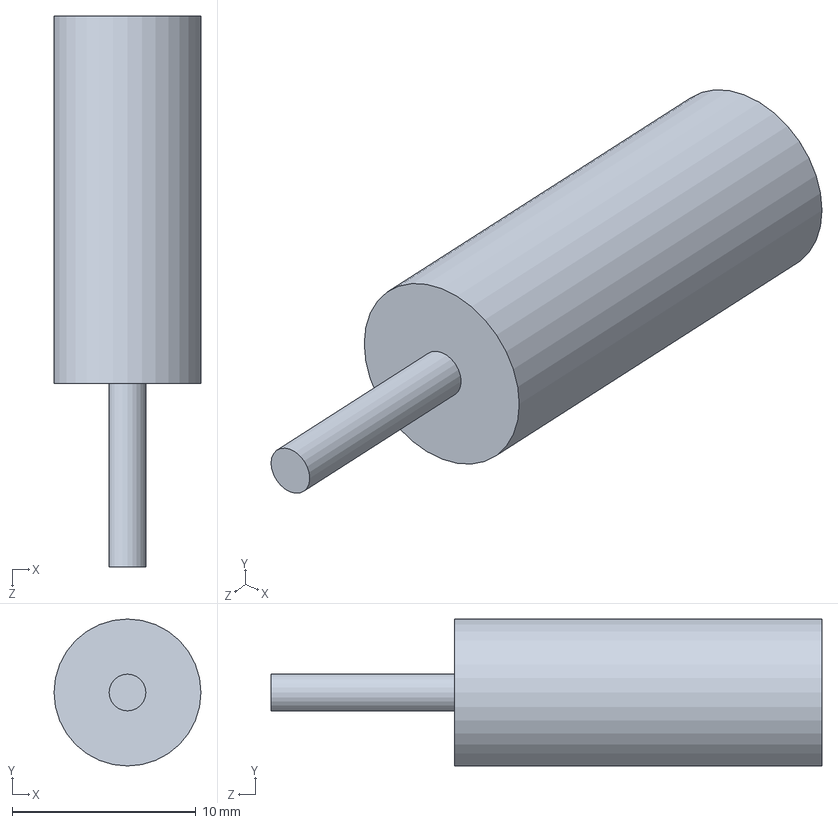
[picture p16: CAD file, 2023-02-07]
CAD/PDR Idea/Motor.SLDPRT
8.00 x 8.00 x 30.0 mm

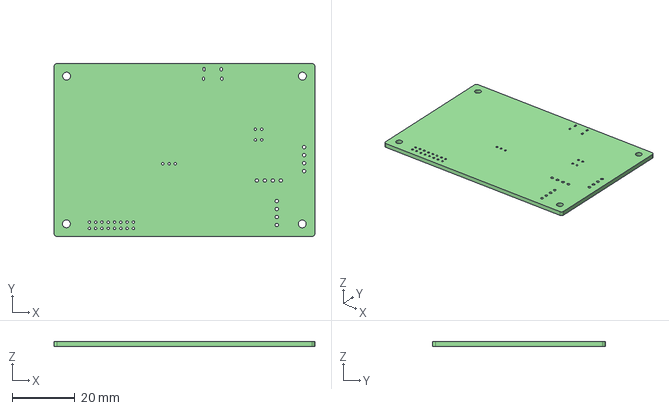
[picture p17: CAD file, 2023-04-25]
Electrical/SADA_Board/SADA_Board/SADA_Board.step
83.0 x 55.0 x 1.61 mm

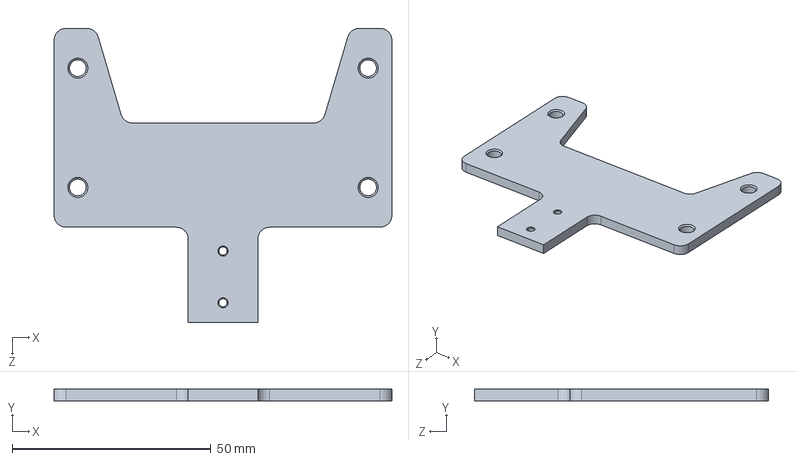
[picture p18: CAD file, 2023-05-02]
CAD/Bracket+Hinge assembly/Array HolderV2.SLDPRT
85.0 x 3.00 x 74.0 mm

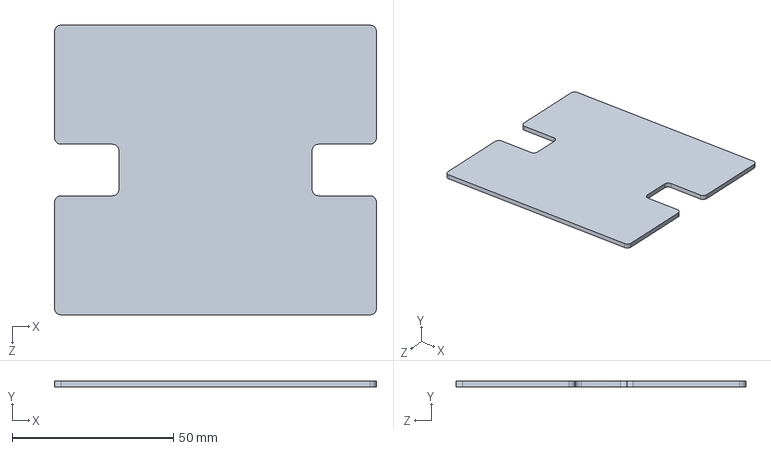
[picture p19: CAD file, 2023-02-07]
CAD/PDR Idea/PCB.SLDPRT
100.0 x 2.00 x 90.0 mm

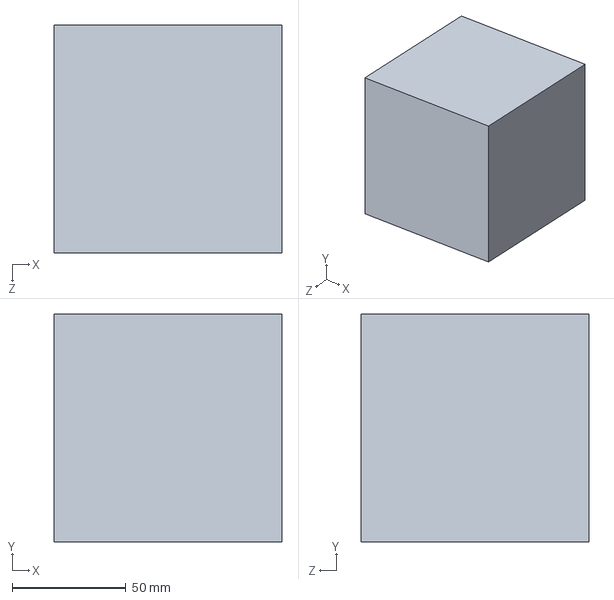
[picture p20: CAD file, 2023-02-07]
CAD/Passive Retainment/CubeSat.SLDPRT
100.0 x 100.0 x 100.0 mm

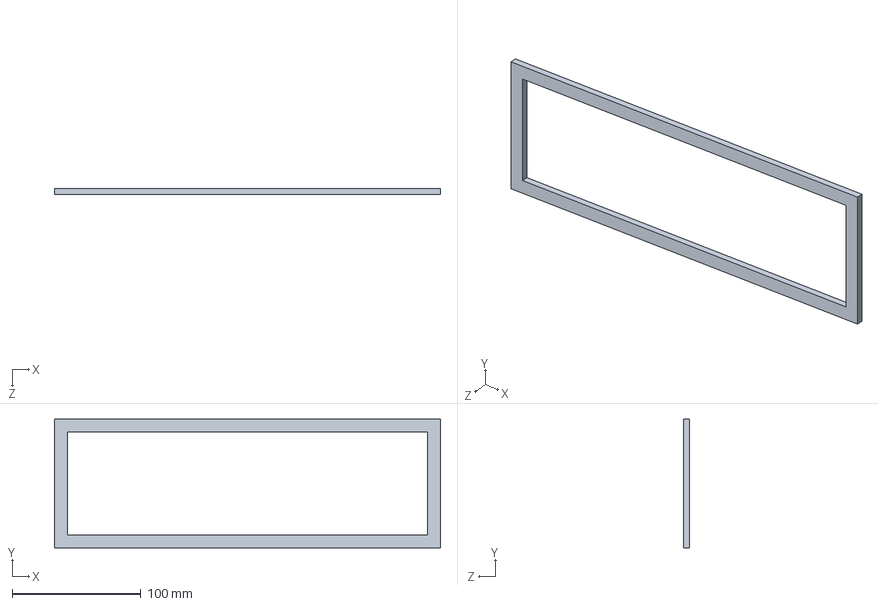
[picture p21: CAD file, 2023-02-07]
CAD/PDR Idea/side panel.SLDPRT
300.0 x 100.0 x 5.00 mm

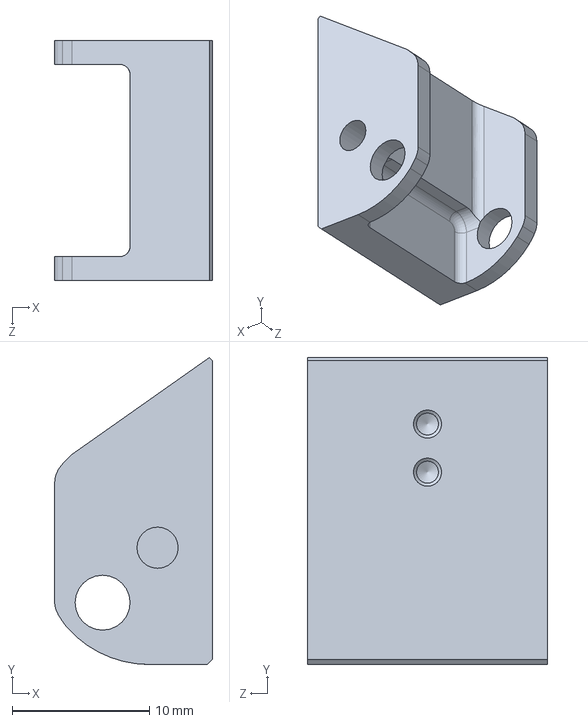
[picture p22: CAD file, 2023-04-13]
CAD/Hinge prototype 1/Swing_Piece_V1.SLDPRT
11.5 x 22.3 x 17.5 mm

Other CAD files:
CAD/Hinge prototype 1/Assembly_V1.SLDASM
CAD/Passive Retainment/Nichrome Wire.SLDPRT
CAD/PDR Idea/Hinge.SLDPRT
CAD/Hinge redesign 2/Swing piece better redesign.SLDPRT
CAD/Hinge prototype 1/9271K88_Torsion Spring.SLDPRT
CAD/Hinge prototype 1/Base_V1.SLDPRT
CAD/Hinge prototype 1/Bolt_mcmaster_V1.SLDPRT
CAD/Hinge prototype 1/Locking_Pin_mcmaster_V1.SLDPRT
CAD/Hinge redesign 2/Base better redesign.SLDPRT
CAD/Hinge redesign 2/Hinge mcmaster 4mm.SLDPRT
CAD/Hinge redesign 2/Hinge.SLDPRT
CAD/Hinge redesign 2/Pin mcmaster.SLDPRT
CAD/Hinge redesign 2/Pin mcmaster_v2.SLDPRT
CAD/Hinge redesign 2/Swing piece better redesign v2.SLDPRT
CAD/Hinge/9657K294_Compression Spring.SLDPRT
CAD/Hinge/Axis Shaft.SLDDRW
CAD/Hinge/Axis Shaft.SLDPRT
CAD/Hinge/Base.SLDDRW
CAD/Hinge/Base.SLDPRT
CAD/Hinge/Hinge ASM.SLDASM
CAD/Hinge/Hinge ASM.SLDDRW
CAD/Hinge/Plunger Button.SLDDRW
CAD/Hinge/Plunger Button.SLDPRT
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

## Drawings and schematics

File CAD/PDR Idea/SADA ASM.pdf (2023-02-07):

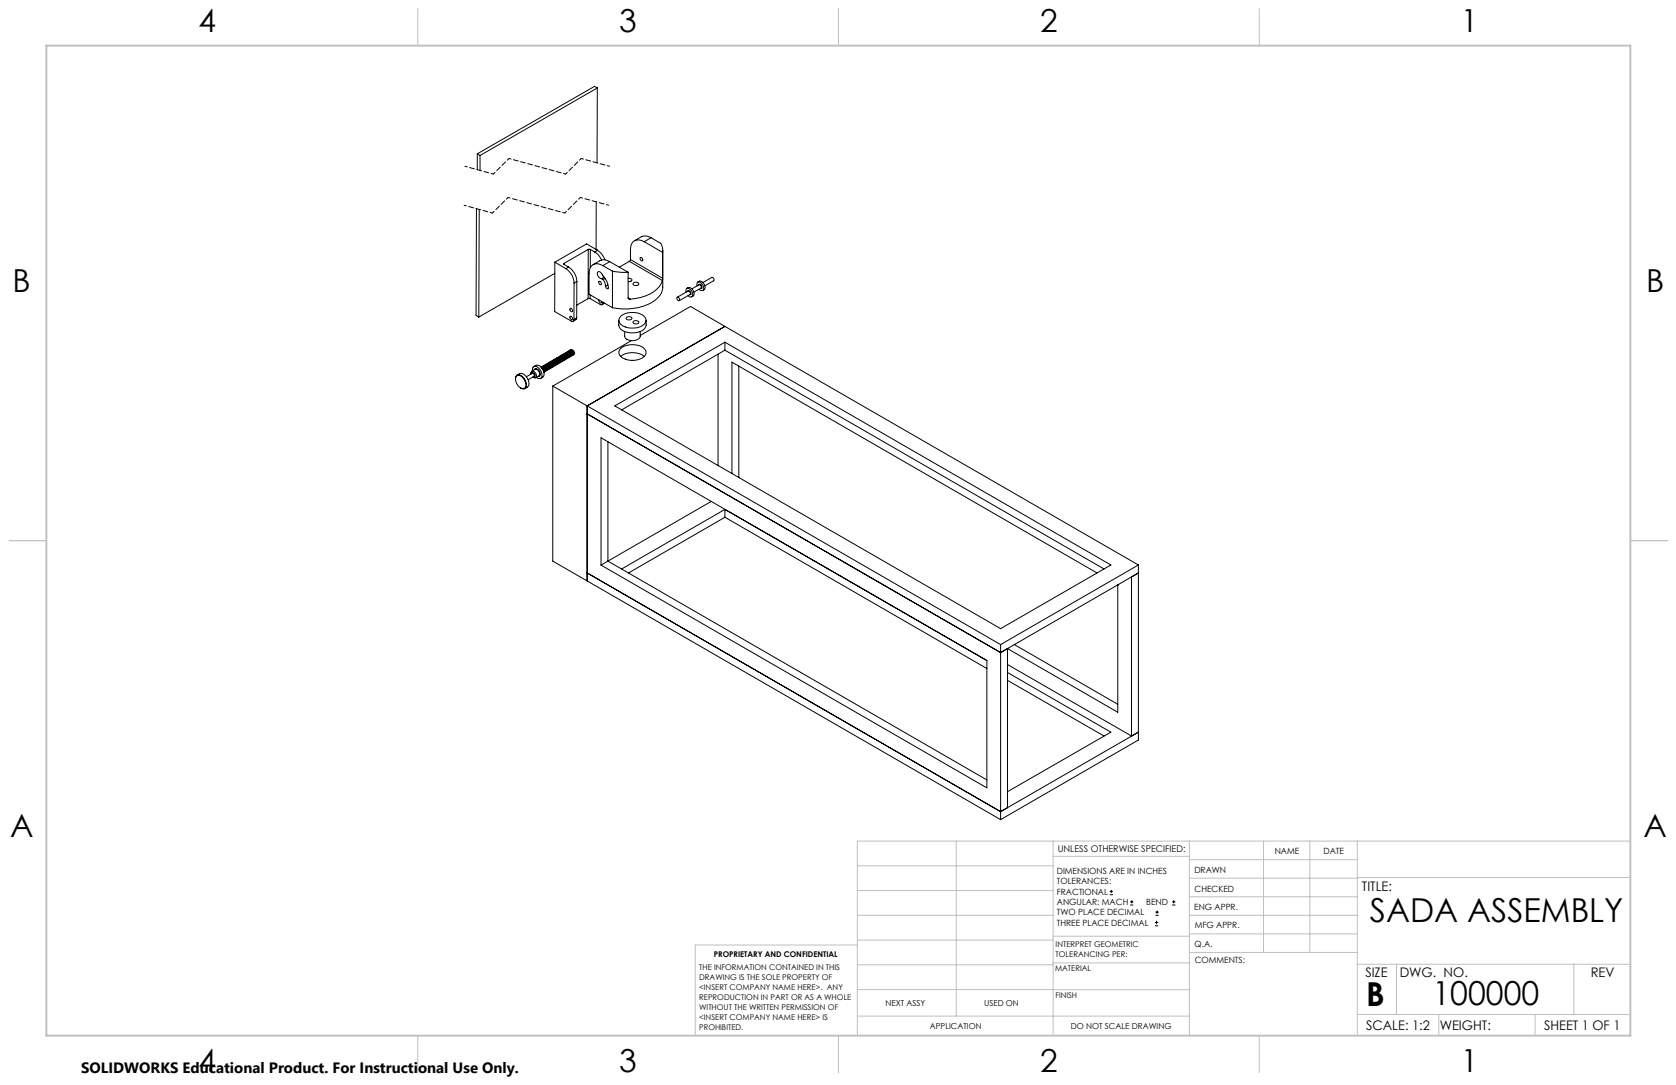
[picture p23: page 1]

UNLESS OTHERWISE SPECIFIED: | | NAME | DATE
DIMENSIONS ARE IN INCHES TOLERANCES: FRACTIONAL ANGULAR: MACH BEND TWO PLACE DECIMAL THREE PLACE DECIMAL | DRAWN

CHECKED | | | TITLE: SADA ASSEMBLY

ENG APPR.
MFG APPR.

INTERPRET GEOMETRIC TOLERANCING PER: | Q.A.
MATERIAL | | SIZE B | DWG. NO. 100000 | REV

PROPRIETARY AND CONFIDENTIAL
THE INFORMATION CONTAINED IN THIS
DRAWING IS THE SOLE PROPERTY OF
<INSERT COMPANY NAME HERE>. ANY
REPRODUCTION IN PART OR AS A WHOLE
WITHOUT THE WRITTEN PERMISSION OF
<INSERT COMPANY NAME HERE> IS
PROHIBITED.

NEXT ASSY | USED ON | FINISH

APPLICATION | DO NOT SCALE DRAWING | | SCALE: 1:2 | WEIGHT: | SHEET 1 OF 1

SOLIDWORKS Educational Product. For Instructional Use Only.

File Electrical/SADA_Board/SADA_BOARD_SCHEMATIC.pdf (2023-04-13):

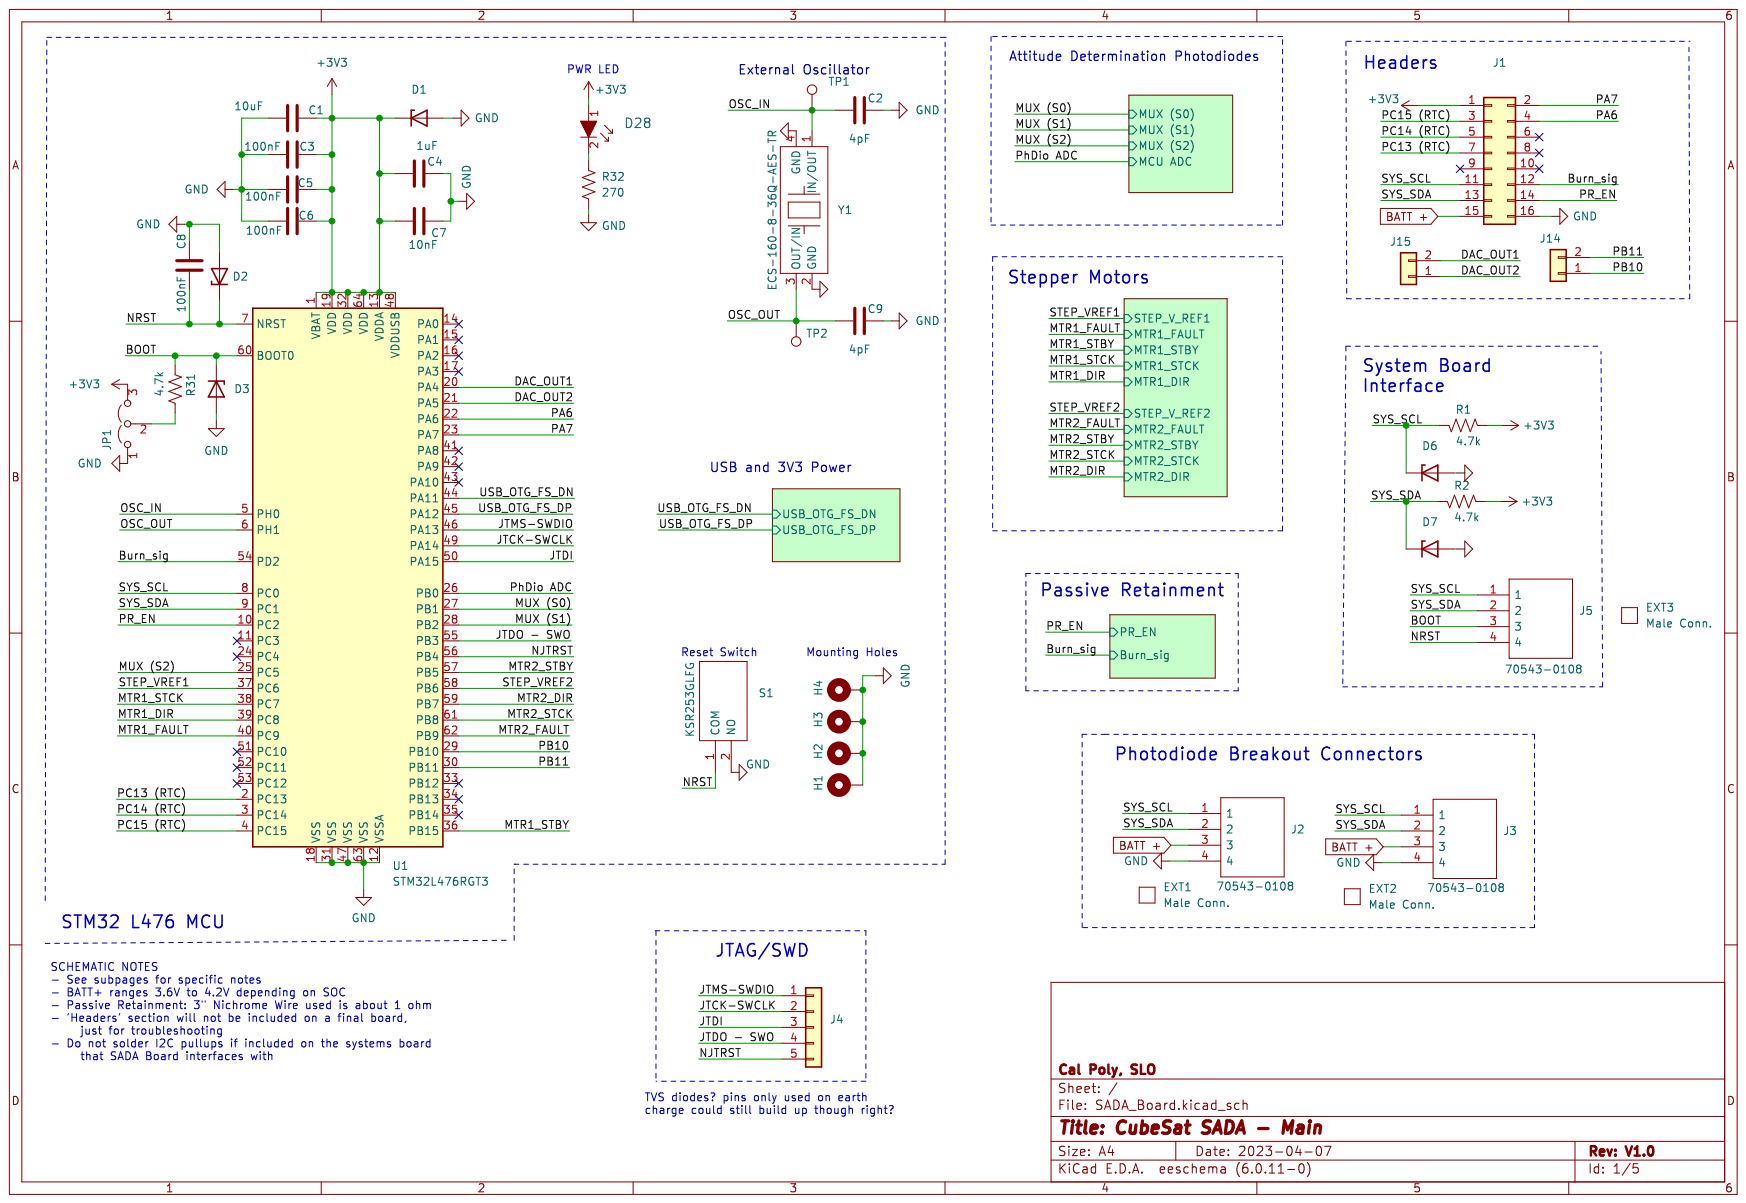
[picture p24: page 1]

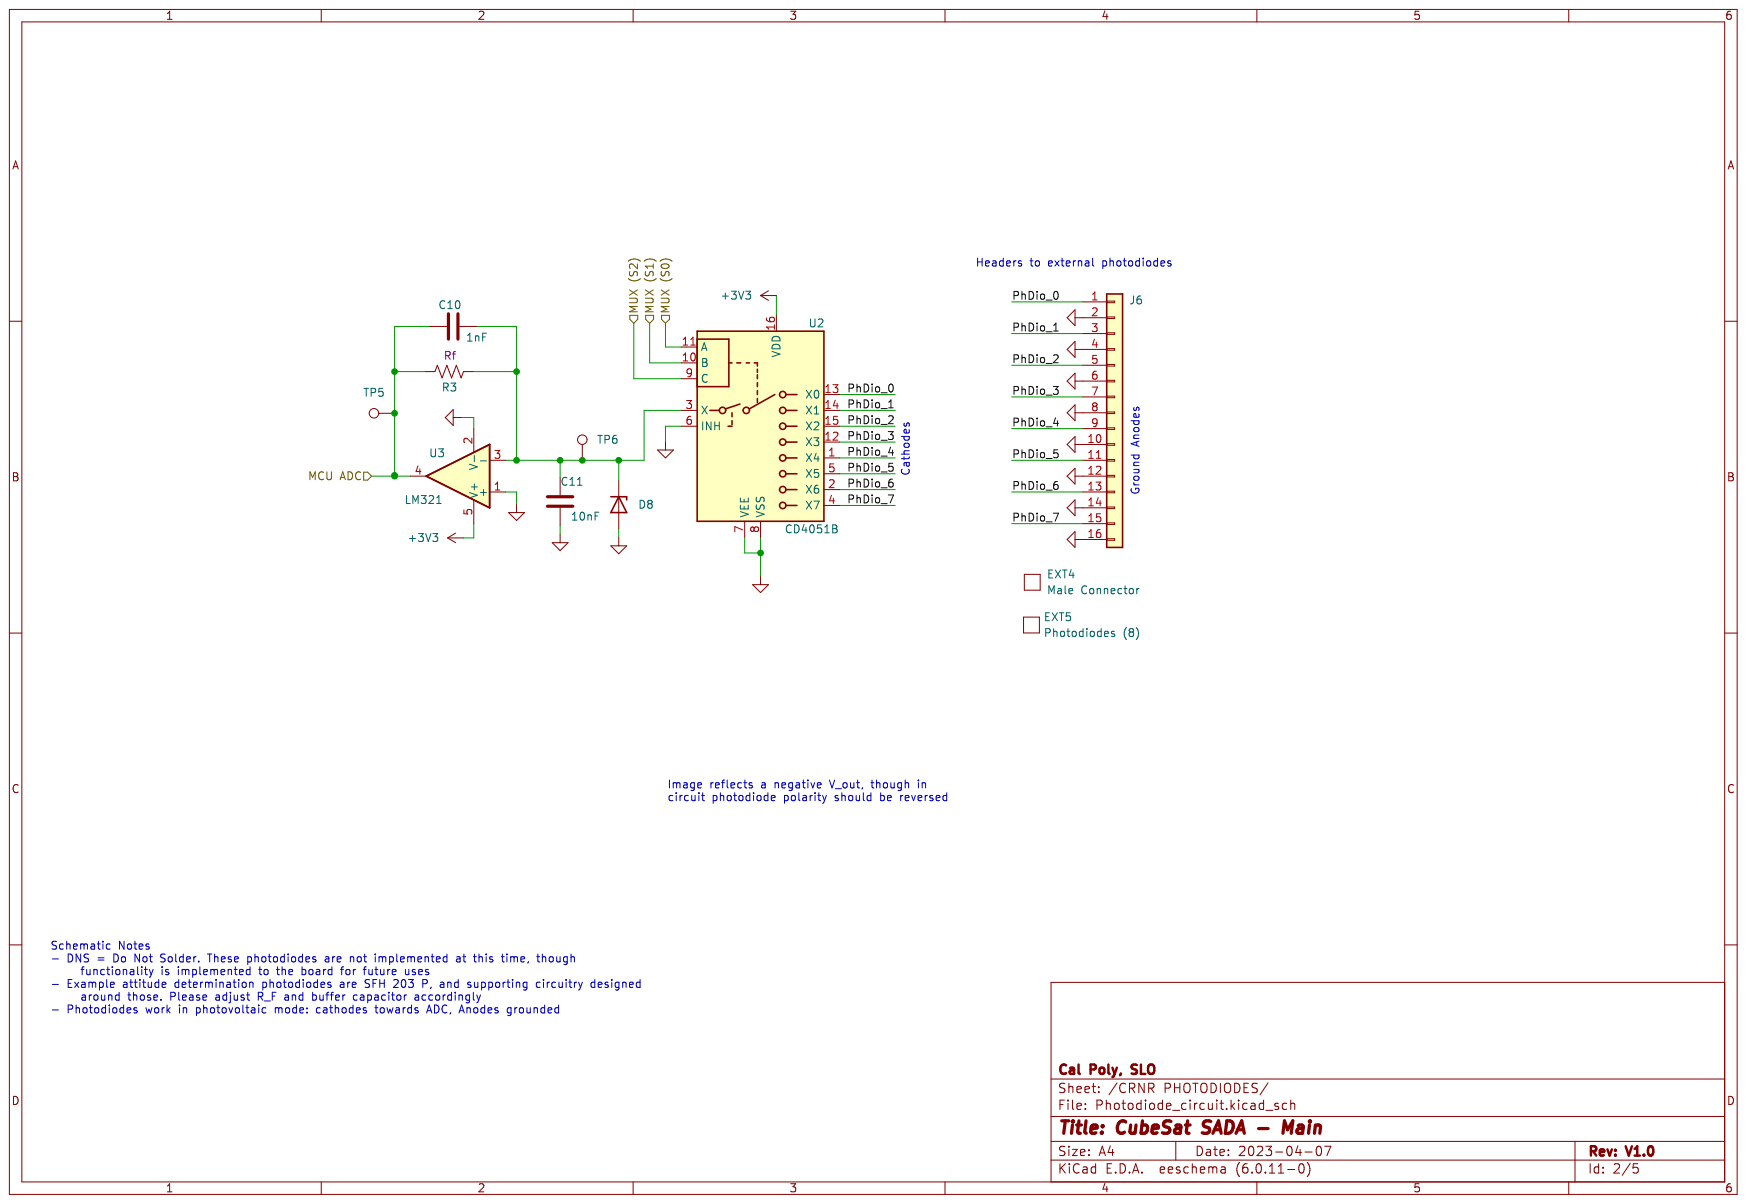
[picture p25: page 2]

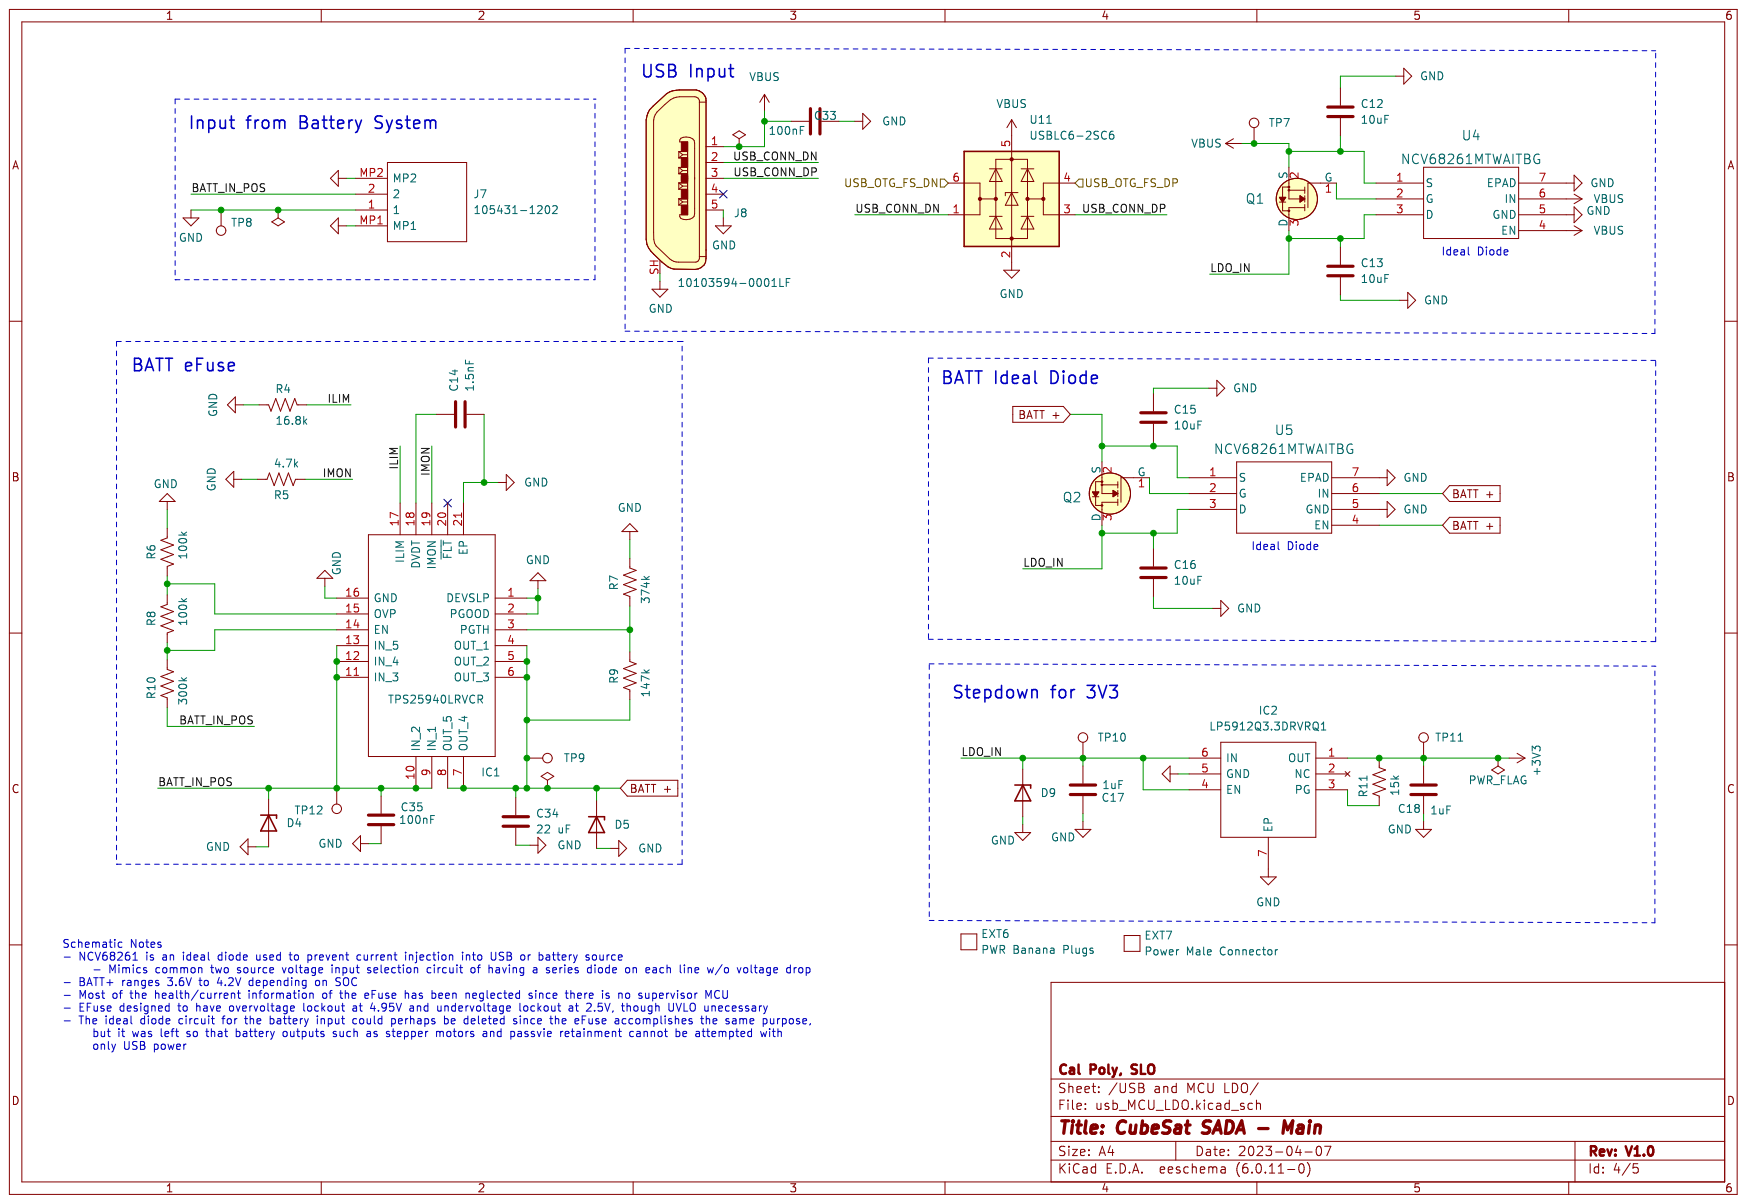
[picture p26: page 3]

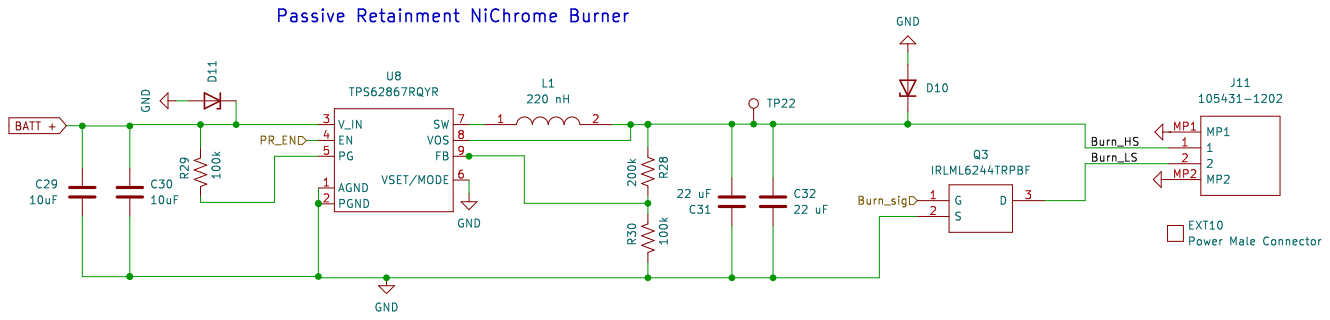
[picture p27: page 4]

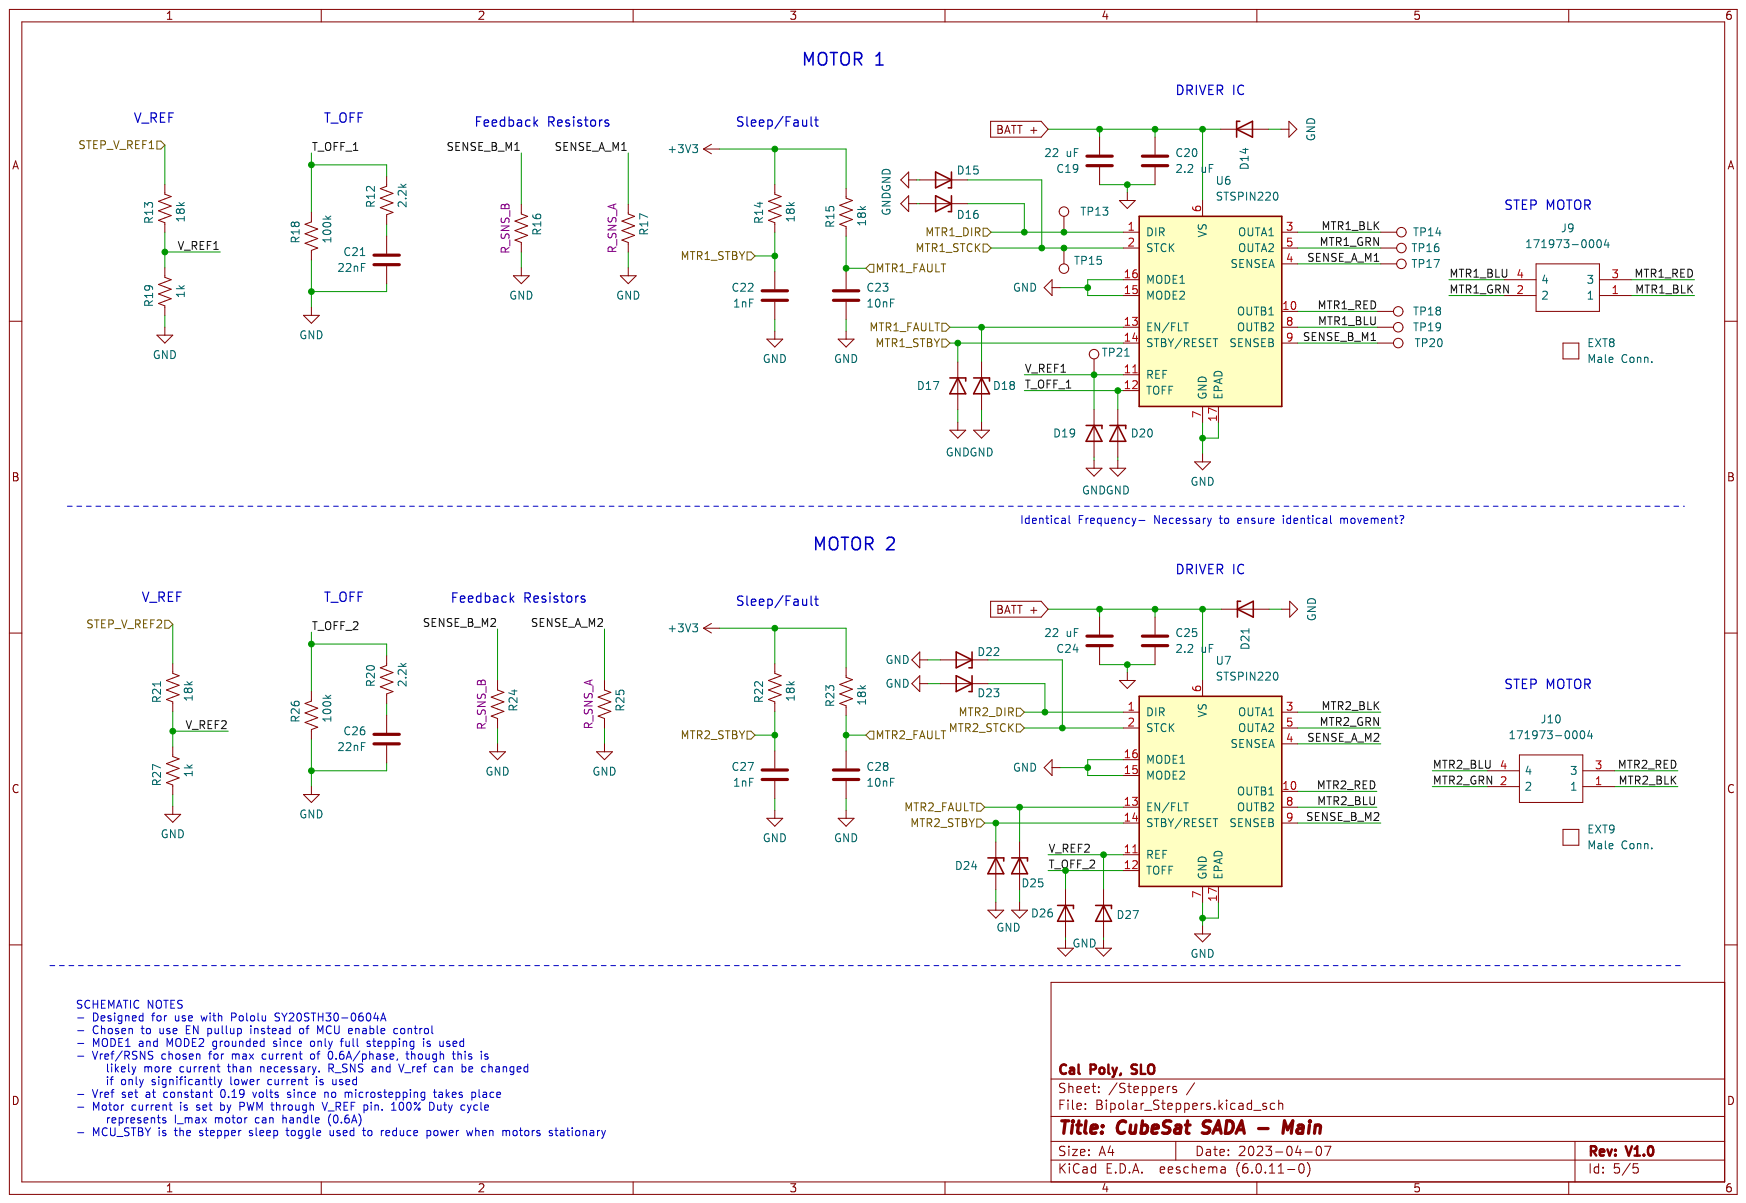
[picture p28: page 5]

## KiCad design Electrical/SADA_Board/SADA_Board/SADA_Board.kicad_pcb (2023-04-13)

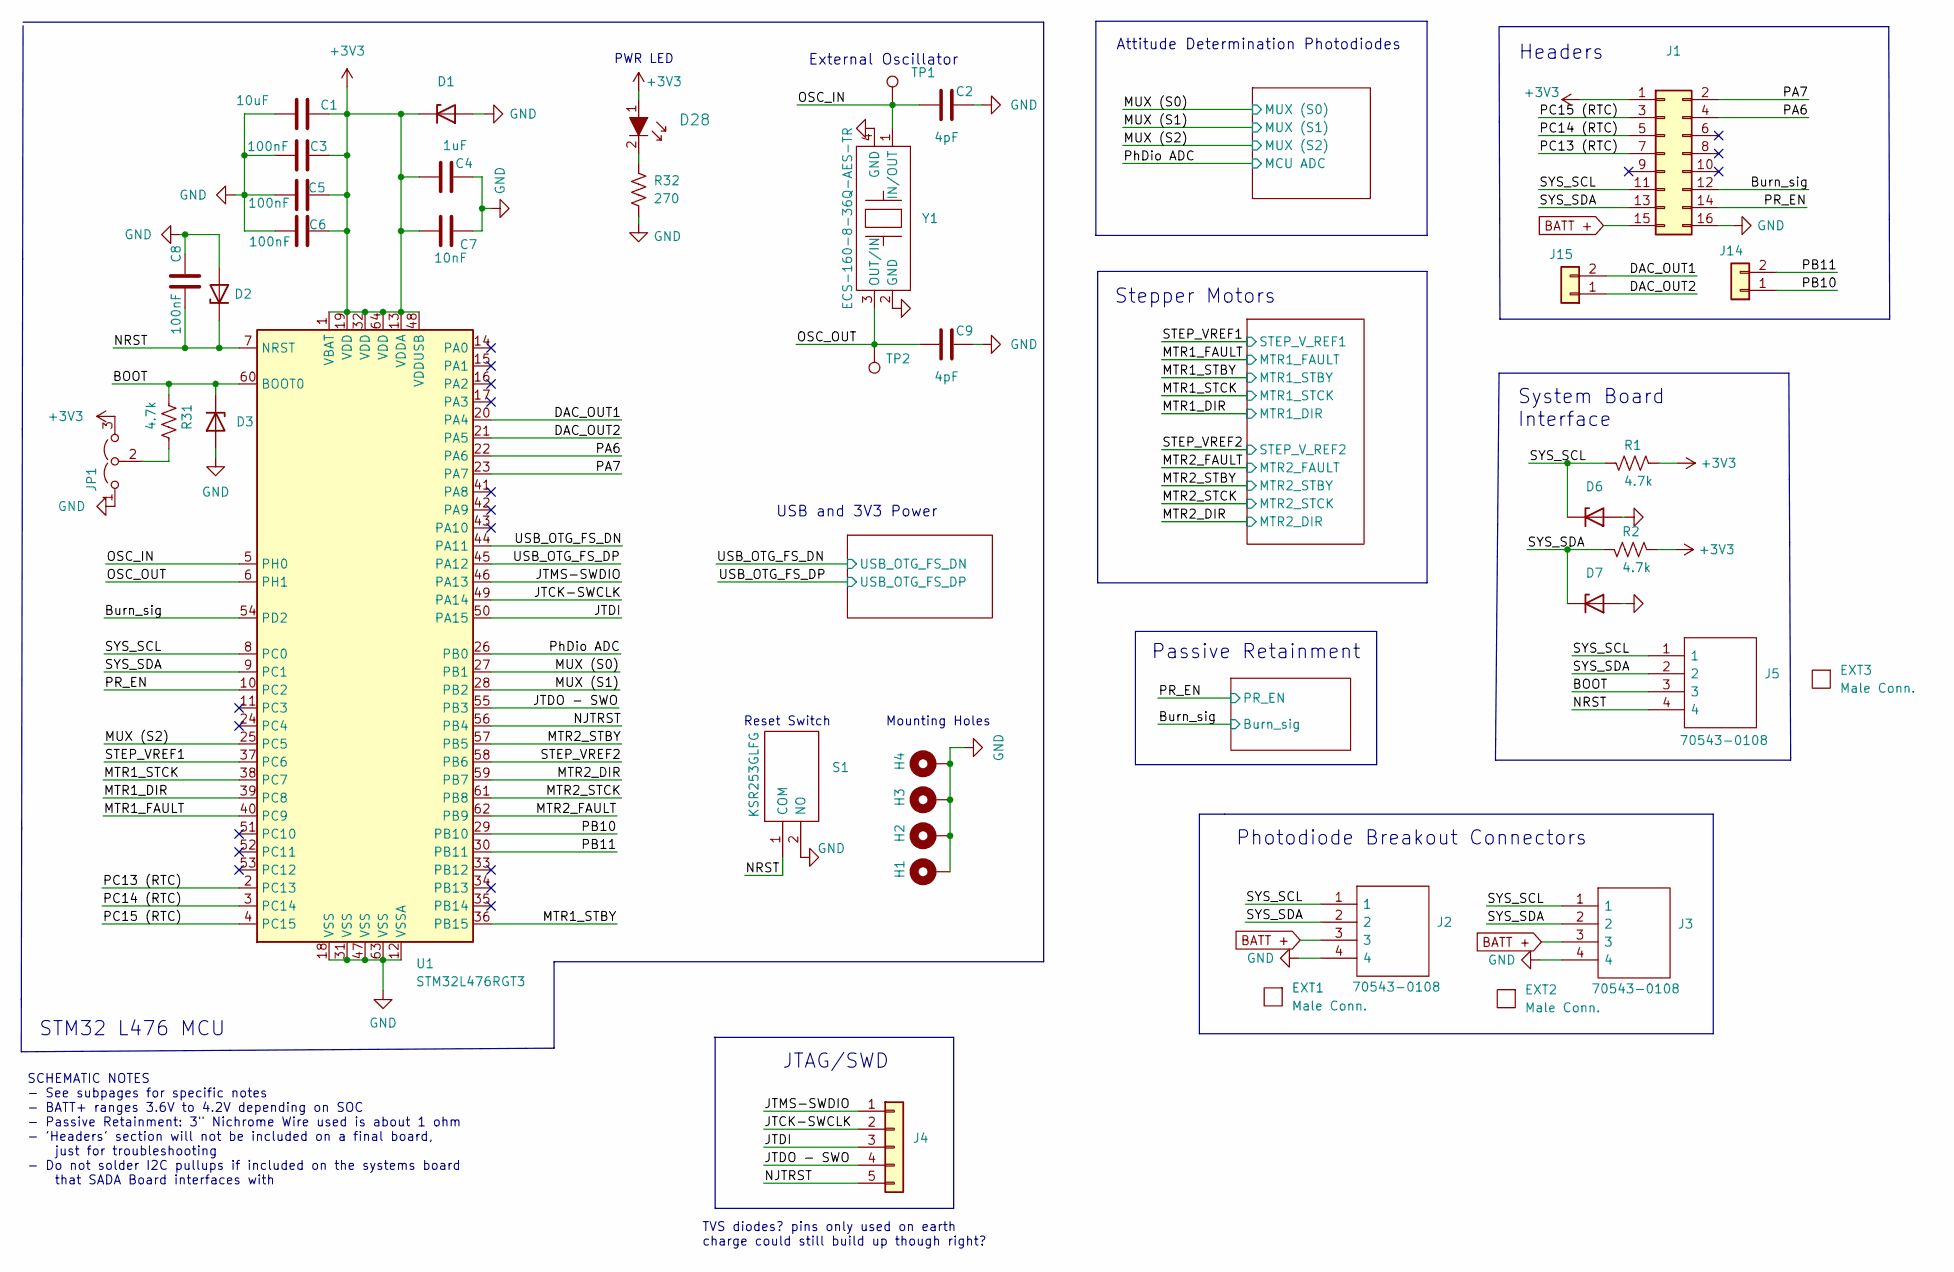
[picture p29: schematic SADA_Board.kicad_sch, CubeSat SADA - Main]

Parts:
C1: 10uF; C_0603_1608Metric; MPN F981A106MMUAJ6
C2, C9: 4pF; C_0402_1005Metric; MPN CGA2B2C0G1H060D050BA
C3, C5, C6, C8: 100nF; C_0402_1005Metric; MPN GRT155R71C104KE01J
C4: 1uF; C_0603_1608Metric; MPN TACL105K016XTA
C7: 10nF; C_0402_1005Metric; MPN GRT155R71C103KE01J
D1, D2, D3, D6, D7: TVS; D_0402_1005Metric; MPN ESD321DPYR
D28: LTST-C193KRKT-5A; LED_0603_1608Metric; MPN LTST-C193KRKT-5A
EXT1, EXT2, EXT3: Male Conn.; EXT_no_footprint; MPN 0014562042
H1, H2, H3, H4: MountingHole_Pad; MountingHole_2.5mm_Pad
J1: Conn_02x08_Odd_Even; PinHeader_2x08_P2.00mm_Vertical; MPN 3-1734506-1
J2, J3, J5: 70543-0108; SHDR4W64P0X254_1X4_1271X508X1181P; Mouser Part Number 538-70543-0108
J4: Conn_01x05; PinHeader_1x05_P2.00mm_Vertical_SMD_Pin1Left; MPN 2PH1-10-UA-SMT-A
J14, J15: Conn_01x02; PinSocket_1x02_P2.00mm_Vertical
JP1: Jumper_3_Open; PinHeader_1x03_P2.00mm_Vertical; MPN 2PH1-10-UA-SMT-A
R1, R2, R31: 4.7k; R_0402_1005Metric; MPN AC0402FR-134K7L
R32: 270; R_0402_1005Metric; MPN CRGCQ0402F270R
S1: KSR253GLFG; Mouser Part Number 611-KSR253G-LFG
TP1, TP2: TestPoint; TestPoint_Pad_D1.0mm
U1: STM32L476RGT3; LQFP-64_10x10mm_P0.5mm; MPN STM32L476RGT3
Y1: ECS-160-8-36Q-AES-TR; XTAL_ECS-160-8-36Q-AES-TR; MPN ECS-160-8-36Q-AES-TR

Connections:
+3V3: C1.1, C3.2, C4.2, C5.2, C6.2, C7.2, D1.1 (K), D28.1, J1.1, JP1.3 (B), R1.1, R2.1, U1.1 (VBAT), U1.13 (VDDA), U1.19 (VDD), U1.32 (VDD), U1.48 (VDDUSB), U1.64 (VDD); also elsewhere on the board
/BOOT: D3.1 (K), J5.3, R31.1, U1.60 (BOOT0)
/Burn_sig: J1.12, U1.54 (PD2); also elsewhere on the board
/DAC_OUT1: J15.2, U1.20 (PA4)
/DAC_OUT2: J15.1, U1.21 (PA5)
/JTCK-SWCLK: J4.2, U1.49 (PA14)
/JTDI: J4.3, U1.50 (PA15)
/JTDO - SWO: J4.4, U1.55 (PB3)
/JTMS-SWDIO: J4.1, U1.46 (PA13)
/MTR1_DIR: U1.39 (PC8); also elsewhere on the board
/MTR1_FAULT: U1.40 (PC9); also elsewhere on the board
/MTR1_STBY: U1.36 (PB15); also elsewhere on the board
/MTR1_STCK: U1.38 (PC7); also elsewhere on the board
/MTR2_DIR: U1.59 (PB7); also elsewhere on the board
/MTR2_FAULT: U1.62 (PB9); also elsewhere on the board
/MTR2_STBY: U1.57 (PB5); also elsewhere on the board
/MTR2_STCK: U1.61 (PB8); also elsewhere on the board
/MUX (S0): U1.27 (PB1); also elsewhere on the board
/MUX (S1): U1.28 (PB2); also elsewhere on the board
/MUX (S2): U1.25 (PC5); also elsewhere on the board
/NJTRST: J4.5, U1.56 (PB4)
/NRST: C8.2, D2.1 (K), J5.4, S1.1 (COM), U1.7 (NRST)
/OSC_IN: C2.2, TP1.1, U1.5 (PH0), Y1.1 (IN/OUT)
/OSC_OUT: C9.2, TP2.1, U1.6 (PH1), Y1.3 (OUT/IN)
/PA6: J1.4, U1.22 (PA6)
/PA7: J1.2, U1.23 (PA7)
/PB10: J14.1, U1.29 (PB10)
/PB11: J14.2, U1.30 (PB11)
/PC13 (RTC): J1.7, U1.2 (PC13)
/PC14 (RTC): J1.5, U1.3 (PC14)
/PC15 (RTC): J1.3, U1.4 (PC15)
/PR_EN: J1.14, U1.10 (PC2); also elsewhere on the board
/PhDio ADC: U1.26 (PB0); also elsewhere on the board
/STEP_VREF1: U1.37 (PC6); also elsewhere on the board
/STEP_VREF2: U1.58 (PB6); also elsewhere on the board
/SYS_SCL: D6.1 (K), J1.11, J2.1, J3.1, J5.1, R1.2, U1.8 (PC0)
/SYS_SDA: D7.1 (K), J1.13, J2.2, J3.2, J5.2, R2.2, U1.9 (PC1)
/USB_OTG_FS_DN: U1.44 (PA11); also elsewhere on the board
/USB_OTG_FS_DP: U1.45 (PA12); also elsewhere on the board
BATT +: J1.15, J2.3, J3.3; also elsewhere on the board
GND: C1.2, C2.1, C3.1, C4.1, C5.1, C6.1, C7.1, C8.1, C9.1, D1.2 (A), D2.2 (A), D3.2 (A), D6.2 (A), D7.2 (A), H1.1, H2.1, H3.1, H4.1, J1.16, J2.4, J3.4, JP1.1 (A), R32.2, S1.2 (NO), U1.12 (VSSA), U1.18 (VSS), U1.31 (VSS), U1.47 (VSS), U1.63 (VSS), Y1.2 (GND), Y1.4 (GND); also elsewhere on the board
unnamed: D28.2, R32.1
unnamed: JP1.2 (C), R31.2

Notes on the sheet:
SCHEMATIC NOTES - See subpages for specific notes - BATT+ ranges 3.6V to 4.2V depending on SOC - Passive Retainment: 3" Nichrome Wire used is about 1 ohm - 'Headers' section will not be included on a final board, just for troubleshooting - Do not solder I2C pullups if included on the systems board 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
TVS diodes? pins only used on earth charge could still build up though right?
Reset Switch
Stepper Motors
Photodiode Breakout Connectors
STM32 L476 MCU
Mounting Holes
Attitude Determination Photodiodes
External Oscillator
JTAG/SWD
Passive Retainment
Headers
PWR LED
System Board Interface
USB and 3V3 Power

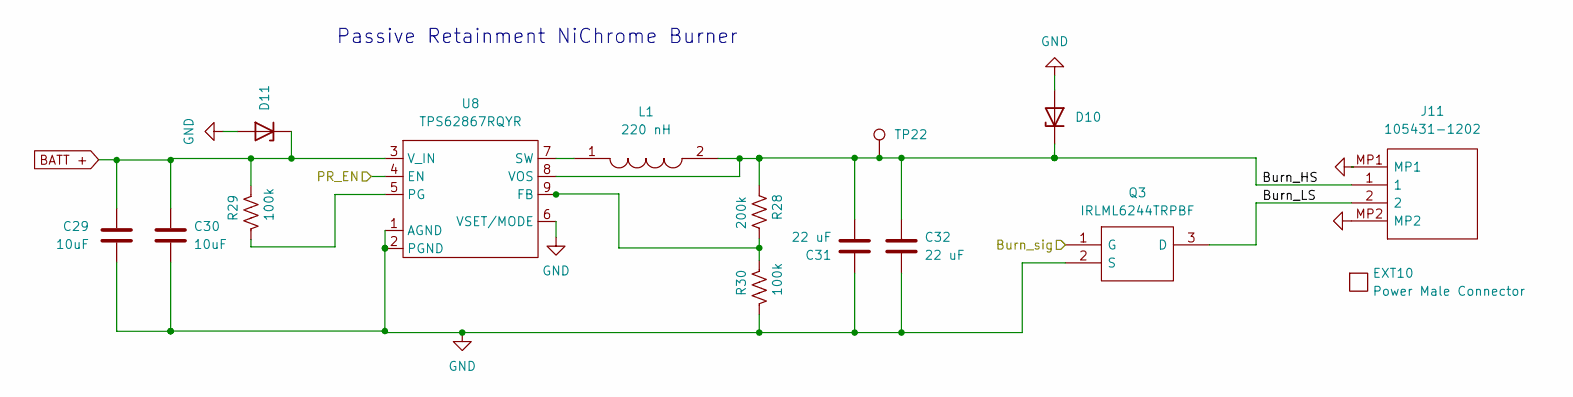
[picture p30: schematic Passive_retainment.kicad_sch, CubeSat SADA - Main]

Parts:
C29, C30: 10uF; C_0603_1608Metric; MPN GRT188C81A106ME13D
C31, C32: 22 uF; C_1210_3225Metric; MPN CGA6P1X7R1C226M250AC
D10, D11: TVS; D_0402_1005Metric; MPN ESD321DPYR
EXT10: Power Male Connector; EXT_no_footprint; MPN 3-640427-2
J11: 105431-1202; 1054311202; Mouser Part Number 538-105431-1202
L1: 220 nH; INDPM3630X150N; Mouser Part Number 70-IHLP1212AEERR22M1
Q3: IRLML6244TRPBF; SOT95P237X112-3N; Mouser Part Number 942-IRLML6244TRPBF
R28: 200k; R_0603_1608Metric_Pad0.98x0.95mm_HandSolder; MPN AC0603FR-07200KL
R29, R30: 100k; R_0402_1005Metric; MPN RMCF0402FT100K
TP22: TestPoint; TestPoint_Pad_D1.0mm
U8: TPS62867RQYR; VQFN-9; MPN TPS62867RQYR

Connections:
/Burn_sig: Q3.1 (G); also elsewhere on the board
/PR_EN: U8.4 (EN); also elsewhere on the board
/Passive Retainment/Burn_HS: C31.2, C32.1, D10.1 (K), J11.1, L1.2, R28.1, TP22.1, U8.8 (VOS)
/Passive Retainment/Burn_LS: J11.2, Q3.3 (D)
BATT +: C29.2, C30.1, D11.1 (K), R29.1, U8.3 (V_IN); also elsewhere on the board
GND: C29.1, C30.2, C31.1, C32.2, D10.2 (A), D11.2 (A), J11.MP1, J11.MP2, Q3.2 (S), R30.2, U8.1 (AGND), U8.2 (PGND), U8.6 (VSET/MODE); also elsewhere on the board
unnamed: L1.1, U8.7 (SW)
unnamed: R28.2, R30.1, U8.9 (FB)
unnamed: R29.2, U8.5 (PG)

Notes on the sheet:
Passive Retainment NiChrome Burner

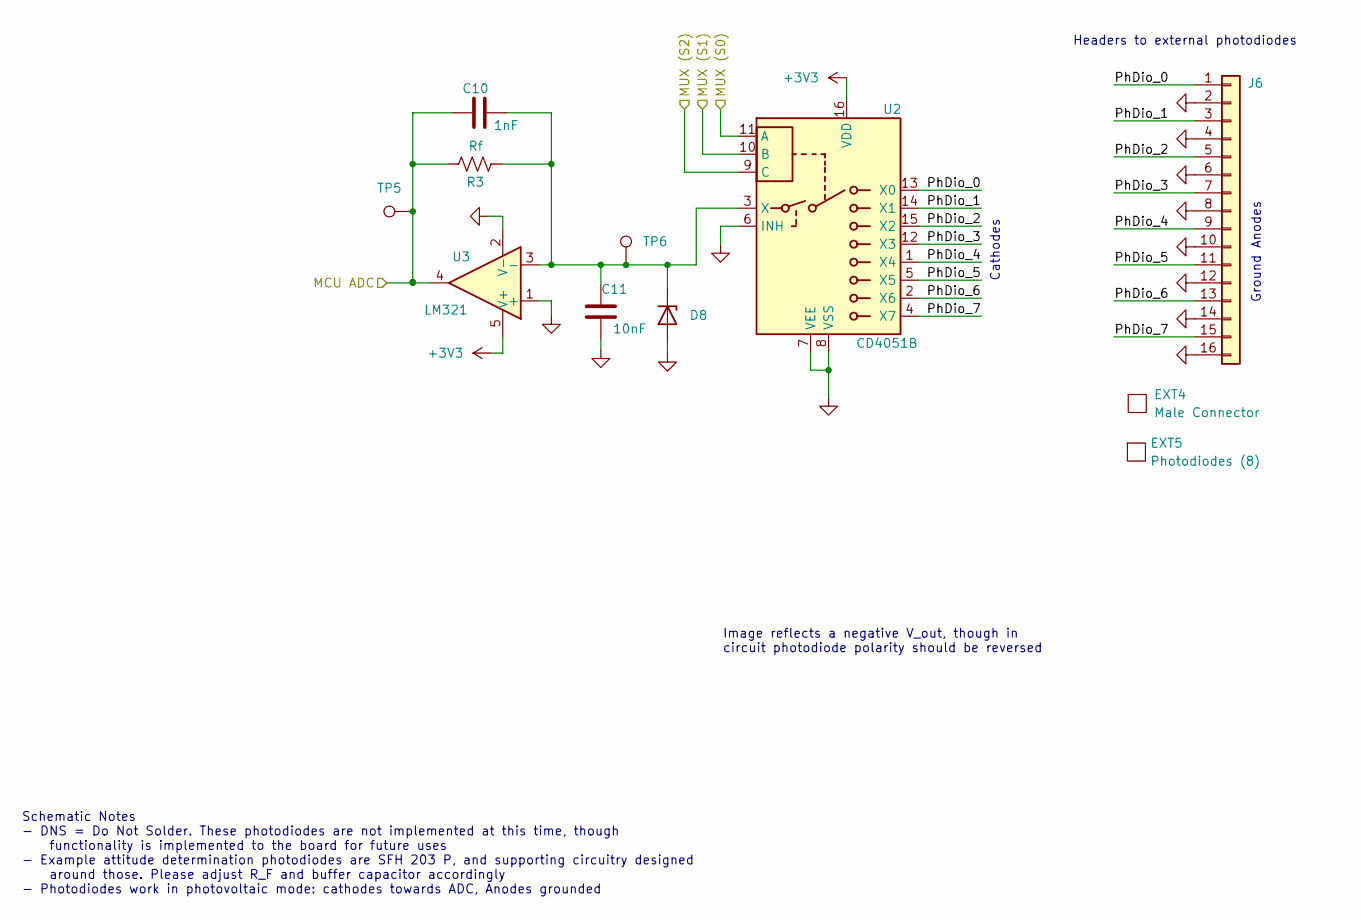
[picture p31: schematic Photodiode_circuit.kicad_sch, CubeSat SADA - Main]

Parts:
C10: 1nF; R_0402_1005Metric; MPN GCM155R71H102KA37J
C11: 10nF; C_0402_1005Metric; MPN GRT155R71C103KE01J
D8: TVS; D_0402_1005Metric; MPN ESD321DPYR
EXT4: Male Connector; EXT_no_footprint; MPN 1-353293-6
EXT5: Photodiodes (8); EXT_no_footprint; MPN SFH 203 P
J6: Conn_01x16; CON16_1X16_DUH_HPI125_TYC; MPN 1-292230-6
R3: 200k; R_0603_1608Metric_Pad0.98x0.95mm_HandSolder; MPN AC0603FR-07200KL
TP5, TP6: TestPoint; TestPoint_Pad_D1.0mm
U2: CD4051B; PW0016A_L; MPN CD4051BQPWRG4Q1
U3: LM321; SOT-23-5; MPN LM321LVIDBVR

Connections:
+3V3: U2.16 (VDD), U3.5 (V+); also elsewhere on the board
/CRNR PHOTODIODES/PhDio_0: J6.1, U2.13 (X0)
/CRNR PHOTODIODES/PhDio_1: J6.3, U2.14 (X1)
/CRNR PHOTODIODES/PhDio_2: J6.5, U2.15 (X2)
/CRNR PHOTODIODES/PhDio_3: J6.7, U2.12 (X3)
/CRNR PHOTODIODES/PhDio_4: J6.9, U2.1 (X4)
/CRNR PHOTODIODES/PhDio_5: J6.11, U2.5 (X5)
/CRNR PHOTODIODES/PhDio_6: J6.13, U2.2 (X6)
/CRNR PHOTODIODES/PhDio_7: J6.15, U2.4 (X7)
/MUX (S0): U2.11 (A); also elsewhere on the board
/MUX (S1): U2.10 (B); also elsewhere on the board
/MUX (S2): U2.9 (C); also elsewhere on the board
/PhDio ADC: U3.4; also elsewhere on the board
GND: C11.2, D8.2 (A), J6.2, J6.4, J6.6, J6.8, J6.10, J6.12, J6.14, J6.16, U2.6 (INH), U2.7 (VEE), U2.8 (VSS), U3.1 (+), U3.2 (V-); also elsewhere on the board
unnamed: C10.1, R3.2, TP5.1
unnamed: C10.2, C11.1, D8.1 (K), R3.1, TP6.1, U2.3 (X), U3.3 (-)

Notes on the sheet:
Headers to external photodiodes
Image reflects a negative V_out, though in circuit photodiode polarity should be reversed
Cathodes
Ground Anodes
Schematic Notes - DNS = Do Not Solder. These photodiodes are not implemented at this time, though functionality is implemented to the board for future uses - Example attitude determination photodiodes are SFH 203 P, and supporting circuitry designed around those. Please adjust R_F and buffer capaci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

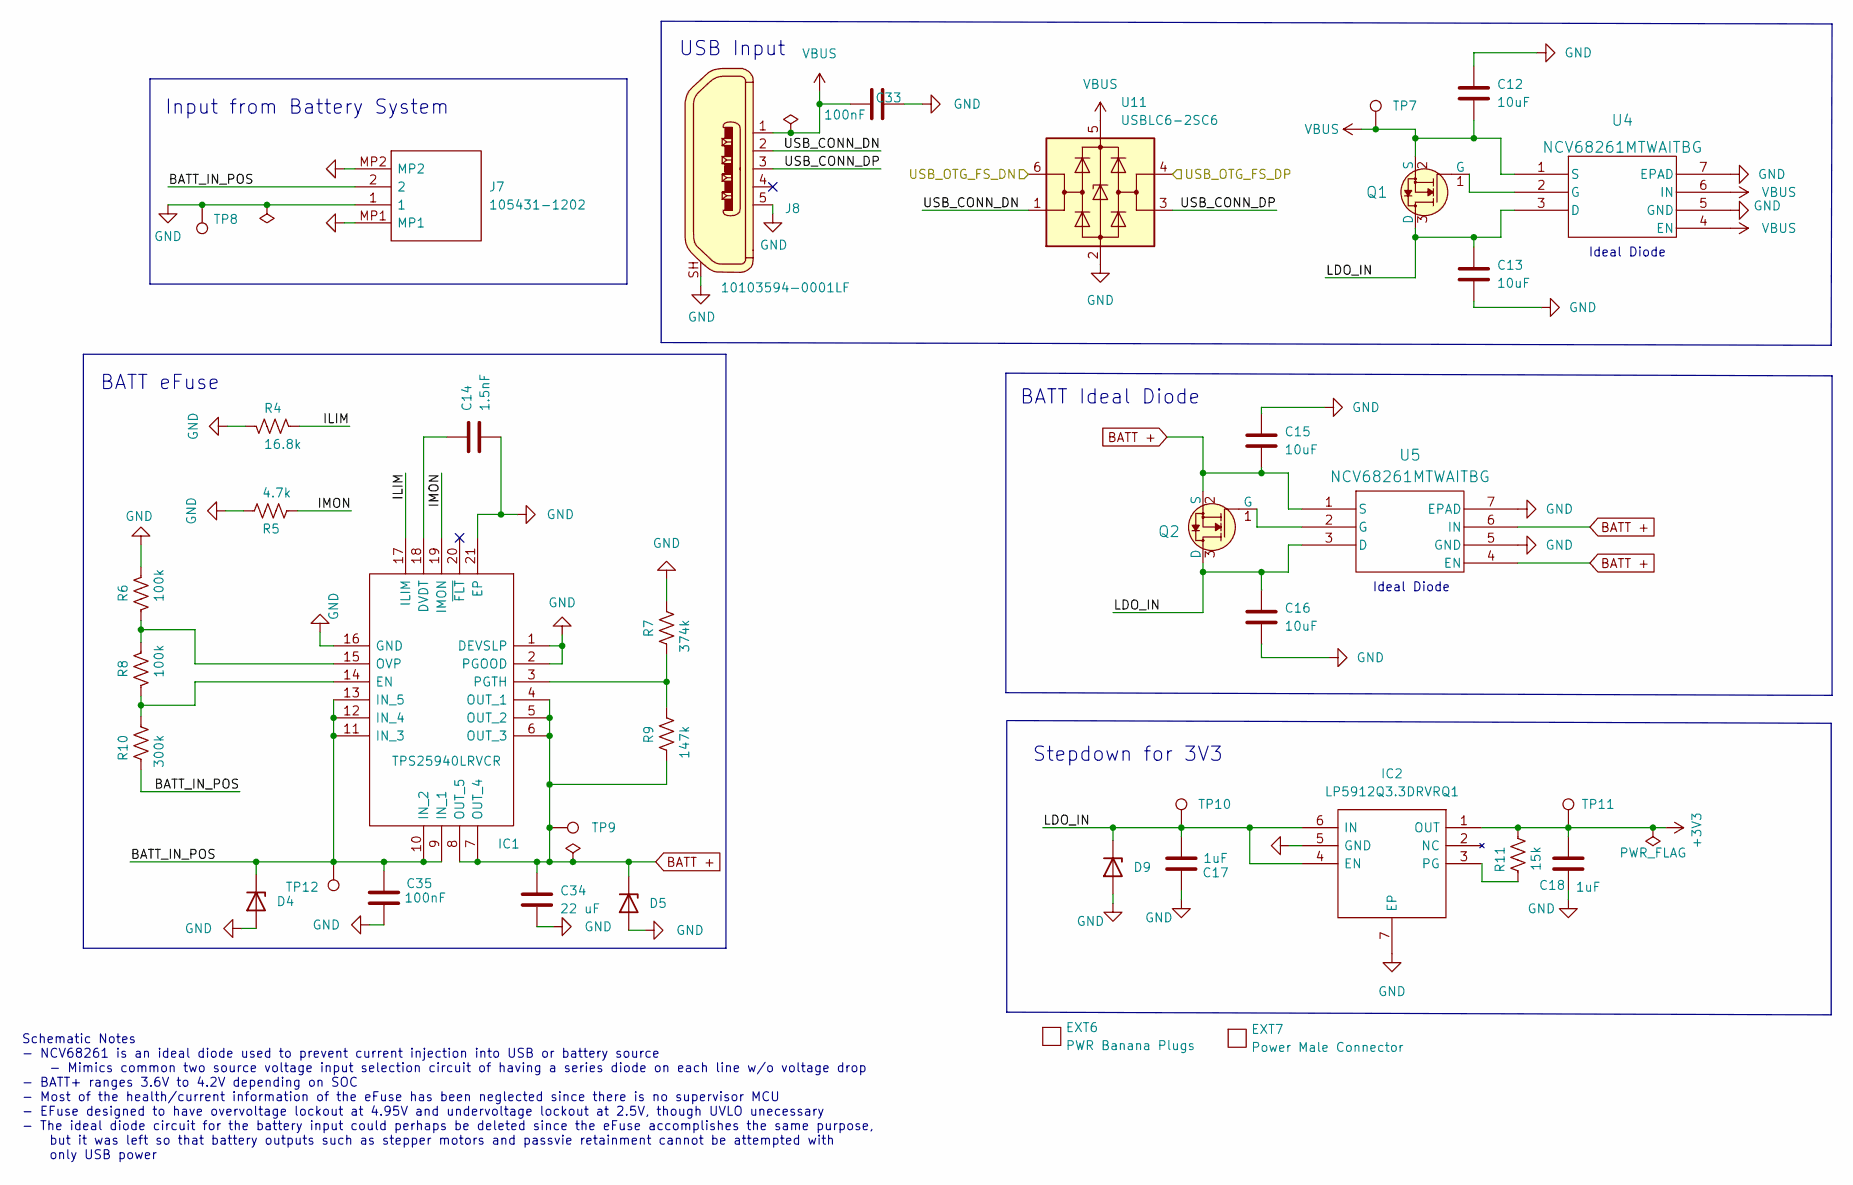
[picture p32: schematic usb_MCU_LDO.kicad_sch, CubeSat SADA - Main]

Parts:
C12, C13, C15, C16: 10uF; C_0603_1608Metric; MPN GRT188C81A106ME13D
C14: 1.5nF; C_0402_1005Metric; MPN CC0402KRX7R7BB152
C17, C18: 1uF; C_0603_1608Metric; MPN TACL105K016XTA
C33, C35: 100nF; C_0402_1005Metric; MPN GRT155R71C104KE01J
C34: 22 uF; C_1210_3225Metric; MPN CGA6P1X7R1C226M250AC
D4, D5, D9: TVS; D_0402_1005Metric; MPN ESD321DPYR
EXT6: PWR Banana Plugs; EXT_no_footprint; MPN 1325-02
EXT7: Power Male Connector; EXT_no_footprint; MPN 3-640427-2
IC1: TPS25940LRVCR; QFN50P300X400X80-21N; Mouser Part Number 595-TPS25940LRVCR
IC2: LP5912Q3.3DRVRQ1; SON65P200X200X80-7N; Mouser Part Number 595-LP5912Q3.3DRVRQ1
J7: 105431-1202; 1054311202; Mouser Part Number 538-105431-1202
J8: 10103594-0001LF; USB_Micro_B_Female_10103594-0001LF; MPN 10103594-0001LF; Digi-Key_PN 609-4050-1-ND
Q1, Q2: NVR5198NLT1G; SOT-23-3; MPN NVR5198NLT1G
R4: 16.8k; R_0402_1005Metric; MPN AC0402FR-0716K9L
R5: 4.7k; R_0402_1005Metric; MPN AC0402FR-134K7L
R6, R8: 100k; R_0402_1005Metric; MPN RMCF0402FT100K
R7: 374k; R_0402_1005Metric; MPN RC0402FR-07374KL
R9: 147k; R_0402_1005Metric; MPN RC0402FR-07147KL
R10: 300k; R_0402_1005Metric; MPN RC0402JR-07300KL
R11: 15k; R_0603_1608Metric; MPN AC0603FR-0715KL
TP7, TP8, TP9, TP10, TP11, TP12: TestPoint; TestPoint_Pad_D1.0mm
U4, U5: NCV68261MTWAITBG; WDFNW6_511DW_ONS_OSI; MPN NCV68261MTWAITBG
U11: USBLC6-2SC6; SOT-23-6; MPN USBLC6-2SC6

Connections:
+3V3: C18.2, IC2.1 (OUT), R11.2, TP11.1; also elsewhere on the board
/USB and MCU LDO/BATT_IN_POS: C35.2, D4.1 (K), IC1.9 (IN_1), IC1.10 (IN_2), IC1.11 (IN_3), IC1.12 (IN_4), IC1.13 (IN_5), J7.2, R10.1, TP12.1
/USB and MCU LDO/ILIM: IC1.17 (ILIM), R4.1
/USB and MCU LDO/IMON: IC1.19 (IMON), R5.1
/USB and MCU LDO/LDO_IN: C13.1, C16.1, C17.2, D9.1 (K), IC2.4 (EN), IC2.6 (IN), Q1.3 (D), Q2.3 (D), TP10.1, U4.3 (D), U5.3 (D)
/USB and MCU LDO/USB_CONN_DN: J8.2, U11.1 (I/O1)
/USB and MCU LDO/USB_CONN_DP: J8.3, U11.3 (I/O2)
/USB_OTG_FS_DN: U11.6 (I/O1); also elsewhere on the board
/USB_OTG_FS_DP: U11.4 (I/O2); also elsewhere on the board
BATT +: C15.2, C34.1, D5.1 (K), IC1.4 (OUT_1), IC1.5 (OUT_2), IC1.6 (OUT_3), IC1.7 (OUT_4), IC1.8 (OUT_5), Q2.2 (S), R9.1, TP9.1, U5.1 (S), U5.4 (EN), U5.6 (IN); also elsewhere on the board
GND: C12.1, C13.2, C14.2, C15.1, C16.2, C17.1, C18.1, C33.2, C34.2, C35.1, D4.2 (A), D5.2 (A), D9.2 (A), IC1.1 (DEVSLP), IC1.2 (PGOOD), IC1.16 (GND), IC1.21 (EP), IC2.5 (GND), IC2.7 (EP), J7.1, J7.MP1, J7.MP2, J8.5, J8.SH, R4.2, R5.2, R6.1, R7.2, TP8.1, U4.5 (GND), U4.7 (EPAD), U5.5 (GND), U5.7 (EPAD), U11.2 (GND); also elsewhere on the board
unnamed: C14.1, IC1.18 (DVDT)
unnamed: IC1.3 (PGTH), R7.1, R9.2
unnamed: IC1.14 (EN), R8.2, R10.2
unnamed: IC1.15 (OVP), R6.2, R8.1
unnamed: IC2.3 (PG), R11.1
unnamed: Q1.1 (G), U4.2 (G)
unnamed: Q2.1 (G), U5.2 (G)
VBUS: C12.2, C33.1, J8.1, Q1.2 (S), TP7.1, U4.1 (S), U4.4 (EN), U4.6 (IN), U11.5 (VBUS)

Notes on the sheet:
Ideal Diode
BATT eFuse
Input from Battery System
Schematic Notes - NCV68261 is an ideal diode used to prevent current injection into USB or battery source - Mimics common two source voltage input selection circuit of having a series diode on each line w/o voltage drop - BATT+ ranges 3.6V to 4.2V depending on SOC - Most of the health/current infor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
Stepdown for 3V3
BATT Ideal Diode
USB Input

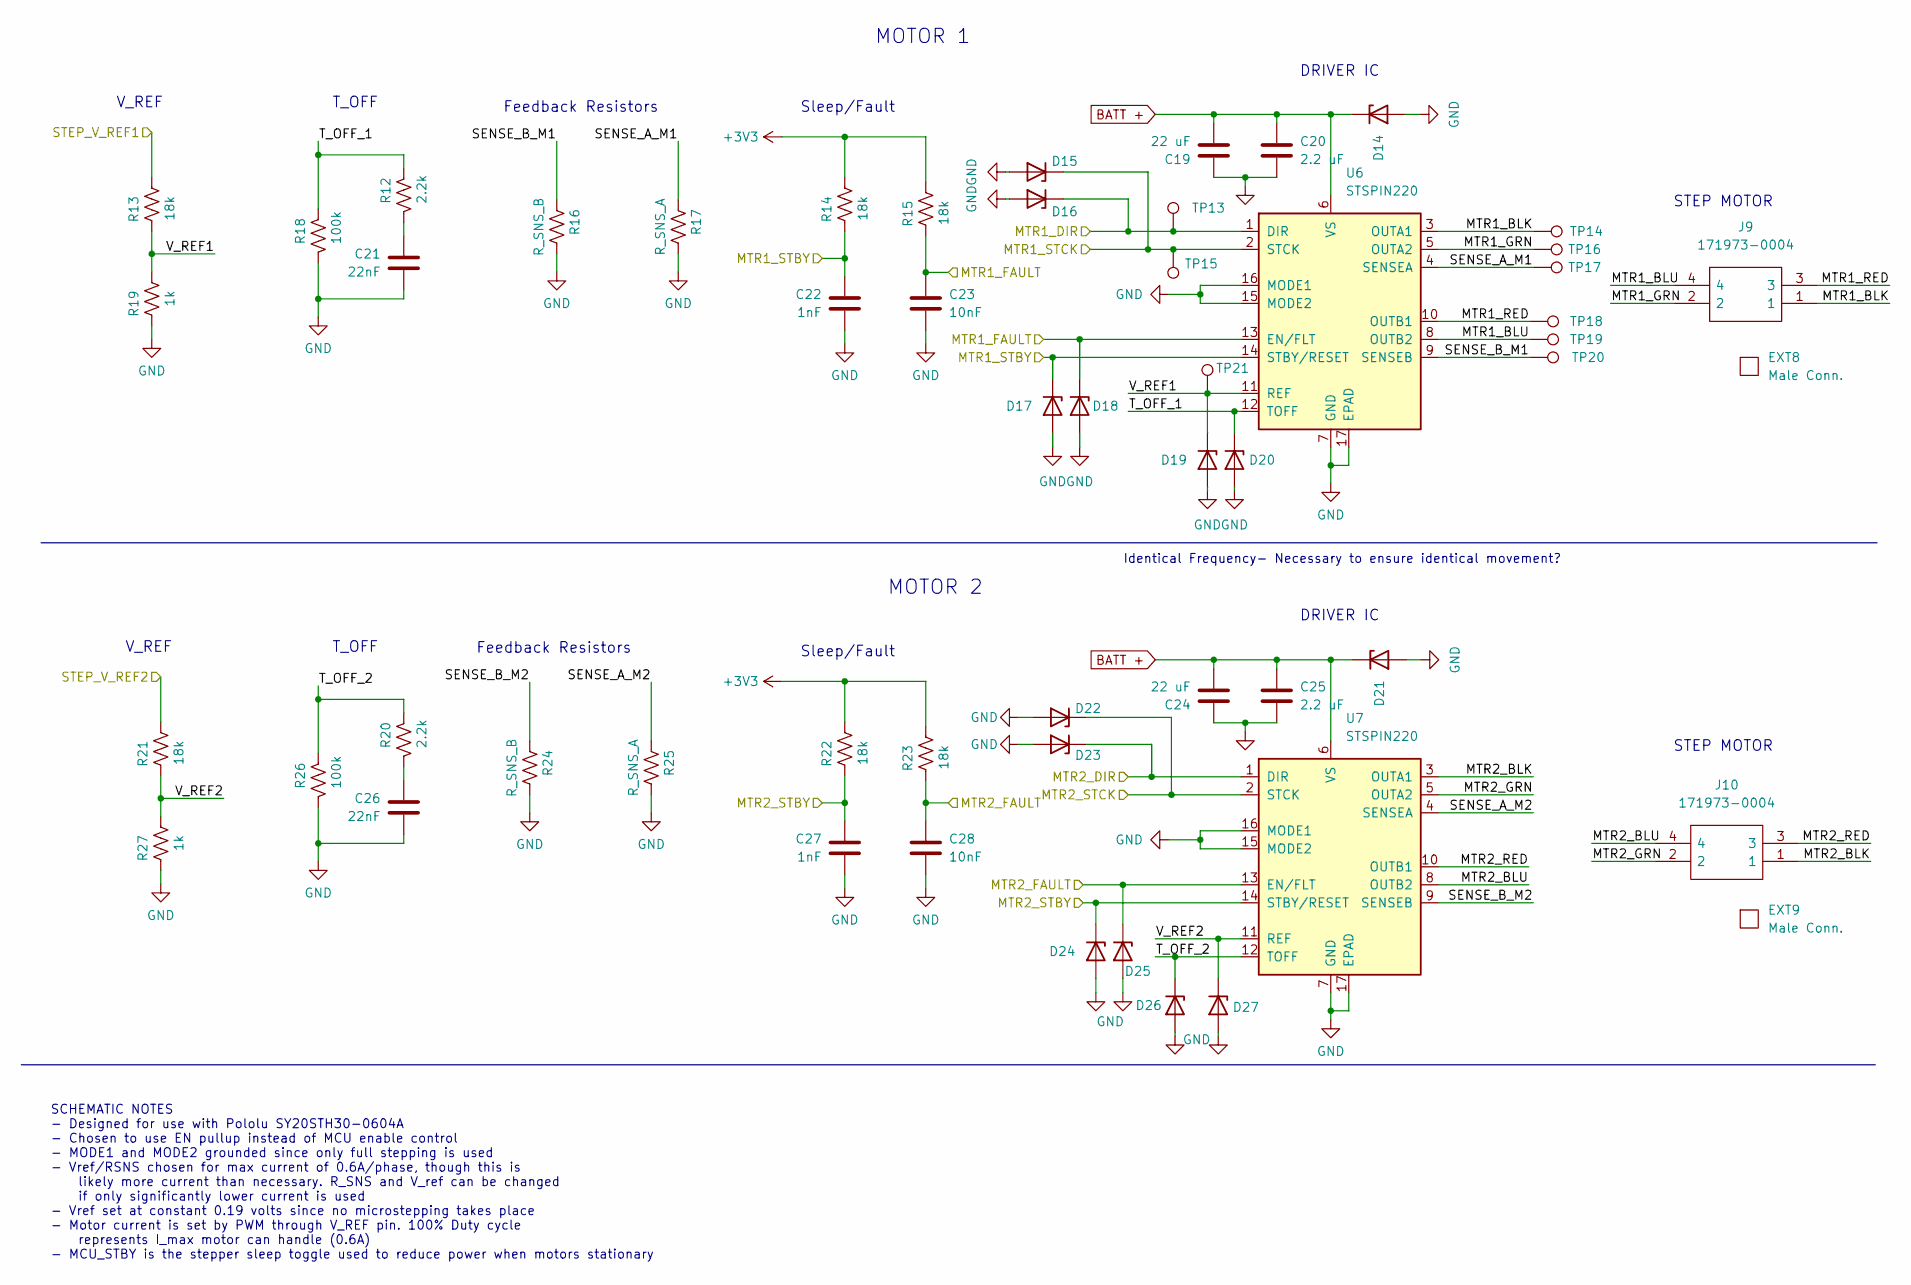
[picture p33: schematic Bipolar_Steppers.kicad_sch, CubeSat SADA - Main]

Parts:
C19, C24: 22 uF; C_1210_3225Metric; MPN CGA6P1X7R1C226M250AC
C20, C25: 2.2 uF; R_0603_1608Metric; MPN CGA3E1X7S1C225M080AC
C21, C26: 22nF; C_0402_1005Metric; MPN AC0402KRX7R7BB223
C22, C27: 1nF; R_0402_1005Metric; MPN GCM155R71H102KA37J
C23, C28: 10nF; R_0402_1005Metric; MPN GRT155R71C103KE01J
D14, D15, D16, D17, D18, D19, D20, D21, D22, D23, D24, D25, D26, D27: TVS; D_0402_1005Metric; MPN ESD321DPYR
EXT8, EXT9: Male Conn.; EXT_no_footprint; MPN 0014562042
J9, J10: 171973-0004; 1719730004; Mouser Part Number 538-171973-0004
R12, R20: 2.2k; R_0402_1005Metric; MPN AC0402FR-072K2L
R13, R14, R15, R21, R22, R23: 18k; R_0402_1005Metric; MPN AC0402FR-0718KL
R16, R17, R24, R25: 330m; R_1206_3216Metric; MPN KRL1632E-M-R330-F-T5
R18, R26: 100k; R_0402_1005Metric; MPN RMCF0402FT100K
R19, R27: 1k; R_0402_1005Metric; MPN AC0402FR-131KL
TP13, TP14, TP15, TP16, TP17, TP18, TP19, TP20, TP21: TestPoint; TestPoint_Pad_D1.0mm
U6, U7: STSPIN220; VQFN-16-1EP_3x3mm_P0.5mm_EP1.8x1.8mm; MPN STSPIN220

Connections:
+3V3: R14.2, R15.2, R22.2, R23.2; also elsewhere on the board
/MTR1_DIR: D16.1 (K), TP13.1, U6.1 (DIR); also elsewhere on the board
/MTR1_FAULT: C23.1, D18.1 (K), R15.1, U6.13 (EN/FLT); also elsewhere on the board
/MTR1_STBY: C22.1, D17.1 (K), R14.1, U6.14 (STBY/RESET); also elsewhere on the board
/MTR1_STCK: D15.1 (K), TP15.1, U6.2 (STCK); also elsewhere on the board
/MTR2_DIR: D23.1 (K), U7.1 (DIR); also elsewhere on the board
/MTR2_FAULT: C28.1, D25.1 (K), R23.1, U7.13 (EN/FLT); also elsewhere on the board
/MTR2_STBY: C27.1, D24.1 (K), R22.1, U7.14 (STBY/RESET); also elsewhere on the board
/MTR2_STCK: D22.1 (K), U7.2 (STCK); also elsewhere on the board
/STEP_VREF1: R13.2; also elsewhere on the board
/STEP_VREF2: R21.2; also elsewhere on the board
/Steppers /MTR1_BLK: J9.1, TP14.1, U6.3 (OUTA1)
/Steppers /MTR1_BLU: J9.4, TP19.1, U6.8 (OUTB2)
/Steppers /MTR1_GRN: J9.2, TP16.1, U6.5 (OUTA2)
/Steppers /MTR1_RED: J9.3, TP18.1, U6.10 (OUTB1)
/Steppers /MTR2_BLK: J10.1, U7.3 (OUTA1)
/Steppers /MTR2_BLU: J10.4, U7.8 (OUTB2)
/Steppers /MTR2_GRN: J10.2, U7.5 (OUTA2)
/Steppers /MTR2_RED: J10.3, U7.10 (OUTB1)
/Steppers /SENSE_A_M1: R17.1, TP17.1, U6.4 (SENSEA)
/Steppers /SENSE_A_M2: R25.1, U7.4 (SENSEA)
/Steppers /SENSE_B_M1: R16.1, TP20.1, U6.9 (SENSEB)
/Steppers /SENSE_B_M2: R24.1, U7.9 (SENSEB)
/Steppers /T_OFF_1: D20.1 (K), R12.1, R18.1, U6.12 (TOFF)
/Steppers /T_OFF_2: D26.1 (K), R20.1, R26.1, U7.12 (TOFF)
/Steppers /V_REF1: D19.1 (K), R13.1, R19.2, TP21.1, U6.11 (REF)
/Steppers /V_REF2: D27.1 (K), R21.1, R27.2, U7.11 (REF)
BATT +: C19.2, C20.1, C24.2, C25.1, D14.1 (K), D21.1 (K), U6.6 (VS), U7.6 (VS); also elsewhere on the board
GND: C19.1, C20.2, C21.2, C22.2, C23.2, C24.1, C25.2, C26.2, C27.2, C28.2, D14.2 (A), D15.2 (A), D16.2 (A), D17.2 (A), D18.2 (A), D19.2 (A), D20.2 (A), D21.2 (A), D22.2 (A), D23.2 (A), D24.2 (A), D25.2 (A), D26.2 (A), D27.2 (A), R16.2, R17.2, R18.2, R19.1, R24.2, R25.2, R26.2, R27.1, U6.7 (GND), U6.15 (MODE2), U6.16 (MODE1), U6.17 (EPAD), U7.7 (GND), U7.15 (MODE2), U7.16 (MODE1), U7.17 (EPAD); also elsewhere on the board
unnamed: C21.1, R12.2
unnamed: C26.1, R20.2

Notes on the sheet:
Identical Frequency- Necessary to ensure identical movement?
Feedback Resistors
DRIVER IC
T_OFF
Sleep/Fault
MOTOR 1
STEP MOTOR
MOTOR 2
V_REF
SCHEMATIC NOTES - Designed for use with Pololu SY20STH30-0604A - Chosen to use EN pullup instead of MCU enable control - MODE1 and MODE2 grounded since only full stepping is used - Vref/RSNS chosen for max current of 0.6A/phase, though this is likely more current than necessary. R_SNS and V_ref can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

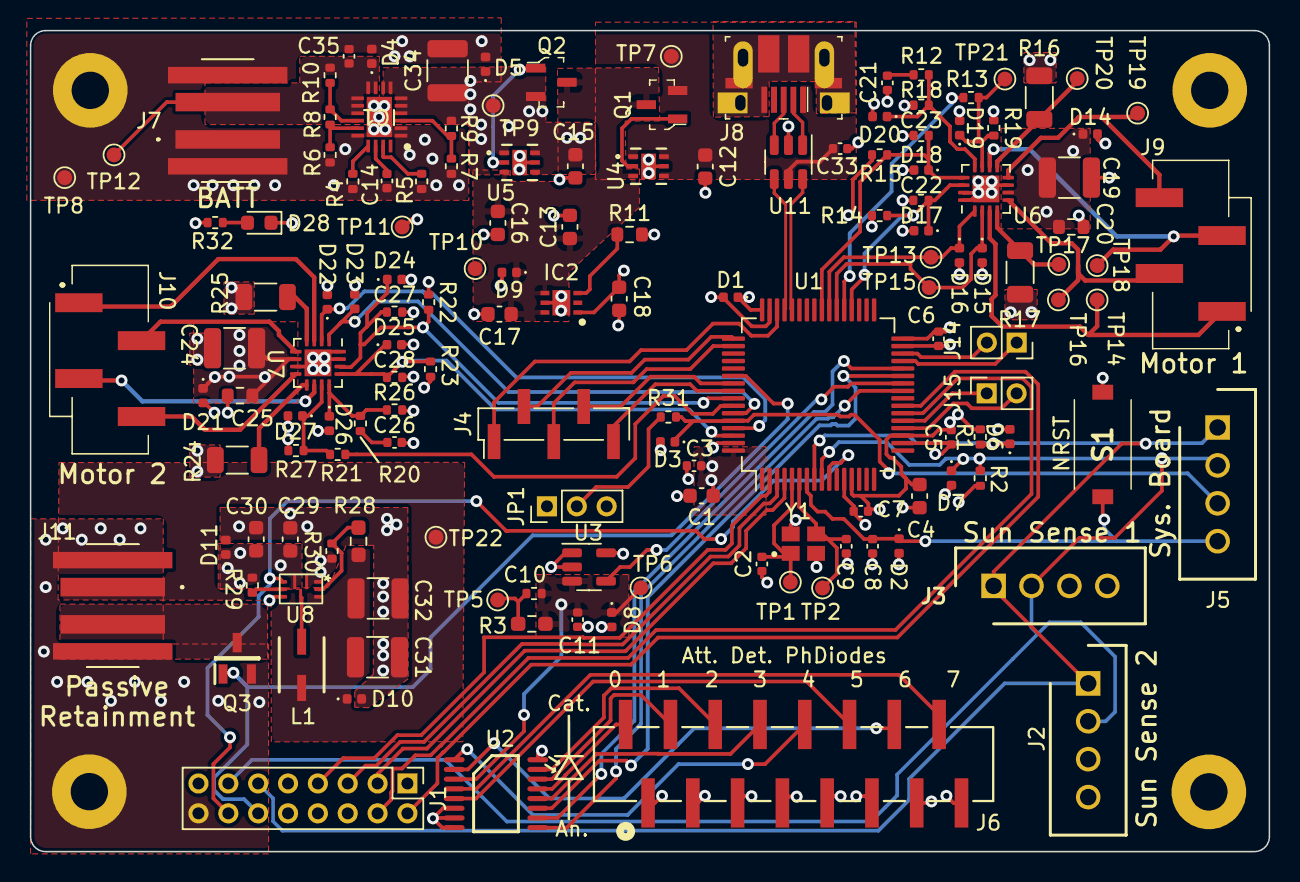
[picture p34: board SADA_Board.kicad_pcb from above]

Board: 4 copper layers, 83.0 x 55.0 mm, 158 parts (0 on the bottom side), 90 nets.

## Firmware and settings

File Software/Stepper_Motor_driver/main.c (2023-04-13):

#include "pico.h"
#include "pico/stdlib.h"
#include <stdio.h>
#include "hardware/gpio.h"
#include "hardware/adc.h"



int main() {

    bool clockwise = false;
    uint8_t full_seq[4] = {};
    uint8_t CW_seq[4] = {9,12,6,3};
    uint8_t CCW_seq[4] = {3,6,12,9};

    if (clockwise) {
        for (int i=0; i < 4; i++) {
            full_seq[i] = CW_seq[i];
        }
    } else {
        for (int i=0; i < 4; i++) {
            full_seq[i] = CCW_seq[i];
        }
    }
    uint8_t gpio_ports[4] = {21,20,19,18};

    uint8_t s;
    uint16_t curr_step = 0;
    const float step_const = 2048/360;

    sleep_ms(3000);

    for (uint8_t i=0; i < 4; i++) {
        gpio_init(gpio_ports[i]);
        gpio_set_dir(gpio_ports[i], GPIO_OUT);
        gpio_put(gpio_ports[i], 0);
    }

    while (curr_step < step_const*360) {
        for (uint8_t i=0; i < 4; i++) {
            s = full_seq[i];

            for (uint8_t b=0; b < 4; b++) {
                uint8_t m = 1 << b;
                if ((m & s) > 0) {
                    gpio_put(gpio_ports[b], 1);
                } else {
                    gpio_put(gpio_ports[b], 0);
                }
            }
            sleep_ms(2);
            curr_step++;
            printf("Step: %f\n",curr_step);
        }
    }
    
}

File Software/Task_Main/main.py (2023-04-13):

from machine import Pin, WDT
from time import sleep
import cotask
import task_share
from stepper import stepper
from atdc import atdc
import _thread


# =============================================================================
# TASK 1 Dual Stepper Motor Driving
# =============================================================================
def Task_1():

    while True:
        # State 0: State Director  
        if state1.get() == 0:
            if mode1.get() == 1:
                state1.put(1)
            elif mode1.get() == 2:
                state1.put(2)
            elif mode1.get() == 3:
                state1.put(3)
            elif mode1.get() == 4:
                state1.put(4)
            elif mode1.get() == 5:
                state1.put(5)
            elif mode1.get() == 6:
                state1.put(6)
            else:
                raise ValueError("Invalid State in Task 1")

        # State 1: Zero Motor 1    
        elif state1.get() == 1:
            complete = mot1.zero(z_flag1.get())
            if complete:
                state1.put(0)
                mode1.put(2)
            else:
                pass
            
        # State 2: Sleep & Sun Tracking Mode Check
        elif state1.get() == 2:
            if track_mode1.get() == 0:
                state1.put(0)
                mode1.put(3)
            elif track_mode1.get() == 1:
                state1.put(0)
                mode1.put(4)
            elif track_mode1.get() == 2:
                state1.put(0)
                mode1.put(5)
            else:
                raise ValueError("Invalid Tracking Mode")

        # State 3: Zero Tracking Mode
        elif state1.get() == 3:
            lost = mot1.zero_tracking()
            if lost:
                state1.put(0)
                mode1.put(1)
            else:
                pass

        # State 4: Constant Uptick Mode
        elif state1.get() == 4:
            reset = mot1.uptick_tracking()
            if reset:
                state1.put(0)
                mode1.put(1)
            else:
                pass

        # State 5: Memory Mode
        elif state1.get() == 5:
            mot1.memory_tracking()
            state1.put(0)
            mode1.put(6)

        # State 6: Dead/Sleep Mode
        elif state1.get() == 6:
            pass


# =============================================================================
# TASK 2 Dual Photodiode ADC Reading
# =============================================================================
def Task_2():
    pass

def button1_cb (GP01):
    print("System Zeroed")
    z_flag1.put(1)
    

def button2_cb (GP02):
    print("System Zeroed")
    z_flag2.put(1)
    

if __name__ == "__main__":
    adc1 = atdc(26,17,16)
    adc2 = atdc(27,2,3)

    mot1 = stepper(21,20,19,18,adc1)
    mot2 = stepper(10,11,12,13,adc2)

    wdt = WDT(timeout=2000)
    # Need to implement wdt.feed() in select locations 

    GP01 = Pin(1,Pin.IN,Pin.PULL_UP)
    GP01.irq(trigger=Pin.IRQ_FALLING, handler=button1_cb)
    GP02 = Pin(2,Pin.IN,Pin.PULL_UP)
    GP02.irq(trigger=Pin.IRQ_FALLING, handler=button2_cb)

    mode1 = task_share.Share ('B', thread_protect = False, name = "Panel 1 Mode-States")
    track_mode1 = task_share.Share ('B', thread_protect = False, name = "Panel 1 Sun Tracking Mode")
    state1 = task_share.Share ('B', thread_protect = False, name = "Panel 1 State")
    z_flag1 = task_share.Share ('B', thread_protect = False, name = "Motor 1 Zeroed Flag")

    mode2 = task_share.Share ('B', thread_protect = False, name = "Panel 2 Mode-States")
    track_mode2 = task_share.Share ('B', thread_protect = False, name = "Panel 2 Sun Tracking Mode")
    state2 = task_share.Share ('B', thread_protect = False, name = "Panel 2 State")
    z_flag2 = task_share.Share ('B', thread_protect = False, name = "Motor 2 Zeroed Flag")

    mode1.put(0)
    track_mode1.put(0)
    state1.put(0)
    z_flag1.put(0)

    mode2.put(0)
    track_mode2.put(0)
    state2.put(0)
    z_flag2.put(0)

    task2 = _thread.start_new_thread(Task_2,())

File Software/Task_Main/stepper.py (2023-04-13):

from machine import Pin
from time import sleep

class stepper:
    def __init__ (self, IN1, IN2, IN3, IN4, adc):
        self.IN1 = Pin(IN1, Pin.OUT) # Step pin 1
        self.IN2 = Pin(IN2, Pin.OUT) # Step pin 2
        self.IN3 = Pin(IN3, Pin.OUT) # Step pin 3
        self.IN4 = Pin(IN4, Pin.OUT) # Step pin 4
        self.adc = adc               # ADC port for photodiode readings
        self.pins = [self.IN1, self.IN2, self.IN3, self.IN4]      # Pin array
        self.CCW_seq = [[0,0,0,1],[0,0,1,0],[0,1,0,0],[1,0,0,0]]  # Bit sequence for counter-clockwise spin
        self.CW_seq = [[1,0,0,0],[0,1,0,0],[0,0,1,0],[0,0,0,1]]   # Bit sequence for clockwise spin
        self.direct_light = 500      # Tested number that represents direct sunlight output of photodiode
        self.pos = 0                 # Absolute position of stepper motor currently
        self.pos1 = 0                # The position of the first value less than direct light in orbit
        self.pos2 = 0                # The position of the last value less than direct light in orbit
        self.first_time = True       # Flag if position 1 has already been determined

# =============================================================================
# Move: Input a target step value for motor to move to.
# =============================================================================
    def move (self,target):
        if target < 0:
            seq = self.CW_seq
            target = -target
        elif target > 0:
            seq = self.CCW_seq
        else:
            pass
        
        curr_step = 0
        while curr_step < target:
            for step in seq:
                for i in range(len(self.pins)):
                    self.pins[i].value(step[i])
                    sleep(0.001)
                curr_step += 1
                self.pos = self.pos + 1

# =============================================================================
# Zero: Find the zero position of the stepper motor with a hall sensor.
# =============================================================================
    def zero (self,z_flag):
        if z_flag == 0:
            self.move(-1)
            return False
        else:
            self.pos = 0
            return True
    
# =============================================================================
# Zero Tracking: Find position of brightness, return to zero when lost.
# =============================================================================
    def zero_tracking(self):
        curr_light = self.adc.read()
        while curr_light <= self.direct_light:
            self.move(1)
        return True

# =============================================================================
# Uptick Tracking: Track the sun by continuing to increase the tick until lost.
# =============================================================================
    def uptick_tracking(self):
        curr_light = self.adc.read()
        if curr_light <= self.direct_light:
            if self.first_time:
                self.pos1 = self.pos
                self.first_time = False
            else:
                self.pos2 = self.pos
            return False
        elif curr_light > self.direct_light and self.pos <= 1024:
            self.move(8)
            return False
        else:
            self.first_time = True
            self.best_pos = (self.pos1 + self.pos2)/2
            return True

# =============================================================================
# Memory Tracking: Remember the best position value from uptick counting and
# go to that value and stay there. 
# =============================================================================
    def memory_tracking(self):
        self.move(self.best_pos)
        

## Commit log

2023-02-01 Datasheet RefDes
    Added reference designators for all data items and added a few more data sheets for the photodiode board
2023-02-01 Photodiode Breakout Board Details
    Added all of the photodiode breakout board files to a new folder
    [Photodiode_Board.kicad_pcb, Photodiode_Board.kicad_sch]
2023-02-01 Stepper Driver Implemented
    Found schematic for stepper motor driver board. Added the model to the current pico shield schematic.
    [pico_shield_ver1.kicad_sch]
2023-02-07 CAD Added
    All Gavin's CAD added to the git in this commit
    [9657K294_Compression Spring.SLDPRT, Array Holder.SLDPRT, Axis Shaft.SLDDRW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]
2023-02-07 ADC Read Script Added
    Simple script written to read ADC values from the Pico. Currently focused on reading temperature sensor values, but can be adapted to read photodiode voltage levels
2023-02-07 I need more commits than Gavin
    [pico_shield_ver1.kicad_sch]
2023-02-12 Almost Complete rough draft
    Doesn't have my custom footprint for components not on PCB, but on BOM such as connectors
    [pico_shield_ver1.kicad_sch]
2023-02-12 Stepper Motor Driver Script Functioning
    Created both C++ and Micropython versions of stepper motor driver. Micropython is significantly easier to implement and work with the controller in real time. I think we make a switch to that
2023-02-20 mo' progress
    [pico_shield_ver1.kicad_sch]
2023-02-21 Draft 1 Schematic, Awaiting Review
    [pico_shield_ver1.kicad_sch]
2023-02-21 Added Custom Symbols and README
    [pico_shield_ver1.kicad_sch]
2023-02-22 Stepper and ADC Classes
    Created classes for driving the stepper motors, along with a class to read values from the adc. Some code has been written in "main.py" for cooperative/preemptive multitasking, however, not quite don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
2023-02-23 Multitasking
    Fixed multitasking with stepper and main
    [main.py, stepper.py]
2023-02-26 Create Hinge redesign
2023-03-08 STM32 and peripherals modification
    [Photodiode_circuit.kicad_sch, SADA_Board.kicad_pcb, SADA_Board.kicad_sch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]
2023-03-09 Partial implementation of stepper motor Step up
    [Photodiode_circuit.kicad_sch, SADA_Board.kicad_sch, Stepper_drivers.kicad_sch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]
2023-03-11 Rough draft stepup done
    [LM5155_56_Quickstart_Calculator_for_Boost_Converter_Design_V1_1_1.xlsx, SADA_Board.kicad_sch, Stepper_drivers.kicad_sch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]
2023-03-15 Pre-regulator/bipolar stepper change
    [SADA_Board.kicad_sch, Stepper_drivers.kicad_sch]
2023-03-21 Connectors, Oscillator
    [Bipolar_Steppers.kicad_sch, LM5155_56_Quickstart_Calculator_for_Boost_Converter_Design_V1_1_1.xlsx, Photodiode_circuit.kicad_sch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]
2023-03-21 Pre-Design Review II
    [Passive_retainment.kicad_sch, Photodiode_circuit.kicad_sch, SADA_Board.kicad_sch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]
2023-03-22 Pre-passive retainment change
    [Passive_retainment.kicad_sch, Photodiode_circuit.kicad_sch, SADA_Board.kicad_sch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]
2023-03-25 pre-gio review
    [Bipolar_Steppers.kicad_sch, Comonent Sheet.xlsx, Passive_retainment.kicad_sch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]
2023-03-28 ESD changes
    [Bipolar_Steppers.kicad_sch, Passive_retainment.kicad_sch, Photodiode_circuit.kicad_sch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]
2023-03-28 layout prog
    [Bipolar_Steppers.kicad_sch, SADA_Board.kicad_pcb, SADA_Board.kicad_sch]
2023-04-06 Layout rough draft
    [Comonent Sheet.xlsx, Passive_retainment.kicad_sch, Photodiode_Board.kicad_sch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]
2023-04-07 V1.0 Finished
    Submitted to manufacturing.
    [Photodiode_circuit.kicad_sch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]
2023-04-07 Updated BOM
    [Bipolar_Steppers.kicad_sch, Passive_retainment.kicad_sch, Photodiode_circuit.kicad_sch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]
2023-04-11 Assembly
    Hinge + solar panel bracket assembly
    [Array HolderV2.SLDPRT, Bracket_Assembly_V1.SLDASM]
2023-04-12 Upd. Schem and Datasheets
    [Bipolar_Steppers.kicad_sch, Photodiode_Board.kicad_sch, SADA_Board.kicad_sch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]
2023-04-13 Hinge + Bracket assembly
    Bracket and assembly
2023-04-13 Updated bracket assembly
    Holes aren't stupid any more
    [Array HolderV2.SLDPRT, Bracket_Assembly_V1.SLDASM]
2023-04-14 PhDio Rough Schem
    [Photodiode_Board.kicad_sch, SADA_Board.step]
2023-04-18 updated cad
    cad
    [Bracket_Assembly_V1.SLDASM]
2023-04-25 updated cad
    stuff
    [Array HolderV2.SLDPRT, Bracket_Assembly_V1.SLDASM]
2023-05-02 Updated Cad
    Updated Cad
    [Bracket_Assembly_V1.SLDASM]
2023-05-16 CAD update
    a
    [Solar Panel + Bracket.SLDPRT]
